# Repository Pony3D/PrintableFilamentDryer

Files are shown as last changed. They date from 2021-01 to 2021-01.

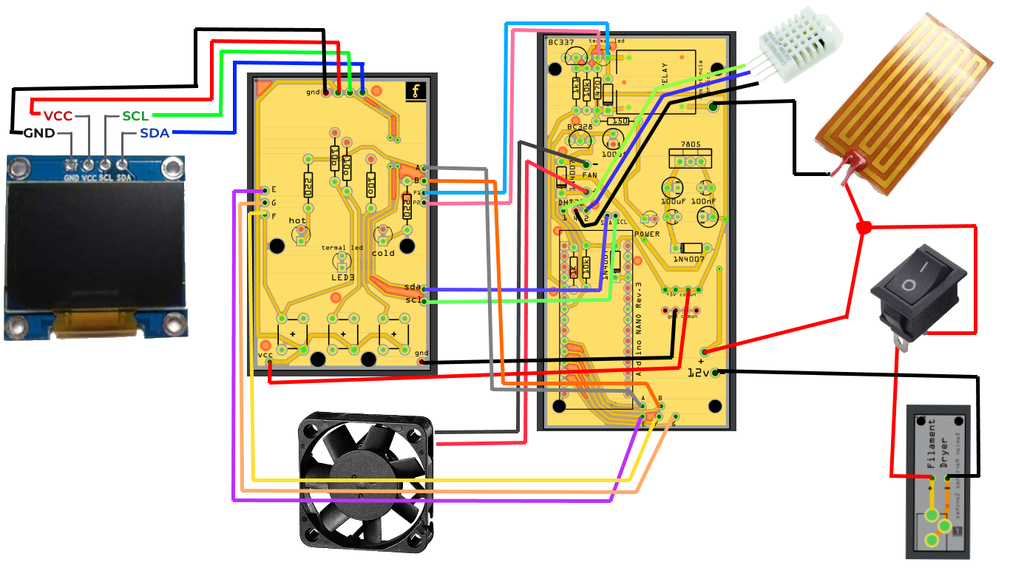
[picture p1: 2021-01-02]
diagrama.png

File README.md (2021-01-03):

# Secador de Filamento Electronico.

Version imprimible de un secador de filamento para impresora 3D.
Modelo optimizado para imprimir en impresora tamaño standar con cama de 220x220, como Ender3.
Es necesario Arduino NANO y conocimientos basicos de electronica.

¿Como funciona?

El secador consta de varias partes que se unen entre si mediante tornillos, ademas de una parte electronica programada en Arduino.
Es recomendable utilizar cables de 1 a 1.3mm maximo de diametro. La electronica es muy simple y cada cable o componente esta marcado con letras y posiciones.

Si se mantiene pulsado el boton +, o el boton -, durante un segundo, se entra en el menu de temperatura, donde se puede configurar la temperatura maxima a alcanzar.
Pulsando repetidas veces sobre + o -, selecionamos la temperatura y pulsando el boton S (Almacenar o Stored), se graba la temperatura de control en la memoria, para el proximo arranque.
El elemento calefactable y el ventilador se encienden si la humedad no esta por debajo del 12%, en el momento que se excede la temperatura maxima grabada en la memoria el elemento calefactable se apaga, no el ventilador.
En el momento que se alcanza un valor de humedad del 12% o inferior, el ventilador y el elemento calefactable se detienen y se muestra, en pantalla, el mensaje de "Secado OK, o DRY OK", y el filamento esta listo para imprimir.
La potencia del elemento calefactable es baja, entorno 14W, por lo que el tiempo de secado del filamento puede ser entorno las 4 horas.
Es recomendable tapar los agujeros exteriores con silicona caliente de los tornillos para mantener la temperatura y humedad correcta del interior.

Componentes necesarios:
- Adaptador de corriente 220v/12v (1.5 a 3A max). https://es.aliexpress.com/item/32859196804.html
- Elemento calefactable de polyamida (12v 14W). https://es.aliexpress.com/item/4000603792416.html
- Interruptor. https://es.aliexpress.com/item/32627544552.html
- Rodamientos de bolas MR106ZZ (6x10x3). https://es.aliexpress.com/item/4000013719586.html
- Ventilador silencioso 40x40x10 12v: https://www.amazon.es/gp/product/B01HTFG9RG/ref=ppx_yo_dt_b_asin_title_o06_s00?ie=UTF8&psc=1
- 0.96" I2C OLED 2 colores. https://es.aliexpress.com/item/1005001392369794.html
- DHT22 (No utilizar DHT11). https://es.aliexpress.com/item/32716996619.html
- Arduino NANO. https://es.aliexpress.com/item/32788387125.html
- Leds de colores: https://es.aliexpress.com/item/32240262628.html
- Conector DC005: https://es.aliexpress.com/item/4000034340966.html
- Rele 5vdc Arduino (sin PCB): https://es.aliexpress.com/item/33032279721.html
- Pulsadores largos: https://es.aliexpress.com/item/32857436208.html

Componentes electronicos PCB 3:
- Power led: 1 Lila o Verde, color a elegir.
- Resistencia: 1K (x2)
- Resistencia: 10K (x2)
- Resistencia: 470 Ohms (x1)
- Resistencia: 150 Ohms (x1)
- Diodo: 14N007 (x3)
- Transistor: BC337 (x1)
- Transistor: BC328 (x1)
- Mosfet: 7805 (x1)
- Condensador ceramico: 100nf (x2)
- Condensador polarizado: 100uf (x2)
- Rele (tipico arduino) 5v 10A.

Componentes electronicos Panel de Control:
- Leds: x1 Rojo, x1 Naranja, x1 Azul.
- Resistencia: 220 Ohms (x2)
- Resistencia: 10 Ohms (x3)
- Pulsadores: (x3)
- Pantalla OLED 0.96": (x1)

LEDS Panel de Control:
- COLD Led: Azul
- HOT Led: Rojo
- LED3 (thermal led): Naranja

Codigo arduino en Español y Ingles, archivos Gerber y Fritzing, diagramas electronicos, componentes necesarios y mas:
https://github.com/Pony3D/PrintableFilamentDryer

¿Donde fabricar las placas PCB?: 
Por ejemplo; https://jlcpcb.com/

ESTE ES UN PROYECTO OPEN SOURCE, POR LO QUE CUALQUIER ELEMENTO ELECTRONICO O DE PROGRAMACION PUEDE SER MODIFICADO Y MEJORADO, EN REALIDAD, ESPERO QUE LO MEJOREIS ;)

NOTA: Las fotografias del modelo expuesta representan un prototipo sobre el que se hicieron las ultimas mejoras, puede ser distinto del modelo final.

///////////////////////////////// ENGLISH TRANSLATION //////////////////////////////////////

# Electronic Filament Dryer.

Printable version of a filament dryer for 3D printer.
Model optimized for printing on a standard size printer with a 220x220 bed, such as Ender3.
Arduino NANO and basic knowledge of electronics are necessary.

How does it work?

The dryer consists of several parts that are joined together by screws, in addition to an electronic part programmed in Arduino.
It is recommended to use cables with a maximum diameter of 1 to 1.3mm. The electronics is very simple and each wire or component is marked with letters and positions.

If you hold down the + button, or the - button, for one second, you enter the temperature menu, where you can set the maximum temperature to be reached.
Pressing repeatedly on + or -, we select the temperature and pressing the S button (Store or Stored), the control temperature is recorded in the memory, for the next start.
The heating element and the fan turn on if the humidity is not below 12%, when the maximum temperature recorded in the memory is exceeded, the heating element turns off, not the fan.
As soon as a humidity value of 12% or less is reached, the fan and the heating element stop and the message "Drying OK, or DRY OK" is displayed on the screen, and the filament is ready to print. .
The power of the heating element is low, around 14W, so the drying time of the filament can be around 4 hours.
It is recommended to cover the outer holes with hot silicone of the screws to maintain the correct temperature and humidity inside.

Required components:
- 220v / 12v power adapter (1.5 to 3A max). https://es.aliexpress.com/item/32859196804.html
- Polyamide heating element (12v 14W). https://es.aliexpress.com/item/4000603792416.html
- Switch. https://es.aliexpress.com/item/32627544552.html
- MR106ZZ ball bearings (6x10x3). https://es.aliexpress.com/item/4000013719586.html
- Silent fan 40x40x10 12v: https://www.amazon.es/gp/product/B01HTFG9RG/ref=ppx_yo_dt_b_asin_title_o06_s00?ie=UTF8&psc=1
- 0.96 "I2C OLED 2 colors. Https://es.aliexpress.com/item/1005001392369794.html
- DHT22 (Do not use DHT11). https://es.aliexpress.com/item/32716996619.html
- Arduino NANO. https://es.aliexpress.com/item/32788387125.html
- Color LEDs: https://es.aliexpress.com/item/32240262628.html
- DC005 connector: https://es.aliexpress.com/item/4000034340966.html
- 5vdc Arduino relay (without PCB): https://es.aliexpress.com/item/33032279721.html
- Long pushbuttons: https://es.aliexpress.com/item/32857436208.html

Electronic components PCB 3:
- Power led: 1 Purple or Green, color to choose.
- Resistance: 1K (x2)
- Resistance: 10K (x2)
- Resistance: 470 Ohms (x1)
- Resistance: 150 Ohms (x1)
- Diode: 14N007 (x3)
- Transistor: BC337 (x1)
- Transistor: BC328 (x1)
- Mosfet: 7805 (x1)
- Ceramic capacitor: 100nf (x2)
- Polarized capacitor: 100uf (x2)
- Relay (typical arduino) 5v 10A.

Electronic components Control Panel:
- Leds: x1 Red, x1 Orange, x1 Blue.
- Resistance: 220 Ohms (x2)
- Resistance: 10 Ohms (x3)
- Buttons: (x3)
- 0.96 "OLED screen: (x1)

LEDS Control Panel:
- COLD Led: Blue
- HOT Led: Red
- LED3 (thermal led): Orange

Arduino code in Spanish and English, Gerber and Fritzing files, electronic diagrams, necessary components and more:
https://github.com/Pony3D/PrintableFilamentDryer

Where to make PCB boards ?:
For example; https://jlcpcb.com/

THIS IS AN OPEN SOURCE PROJECT, SO ANY ELECTRONIC OR PROGRAMMING ELEMENTS CAN BE MODIFIED AND IMPROVED, IN REALITY, I HOPE YOU WILL IMPROVE IT;)

NOTE: The photographs of the exposed model represent a prototype on which the last improvements were made, it may be different from the final model.

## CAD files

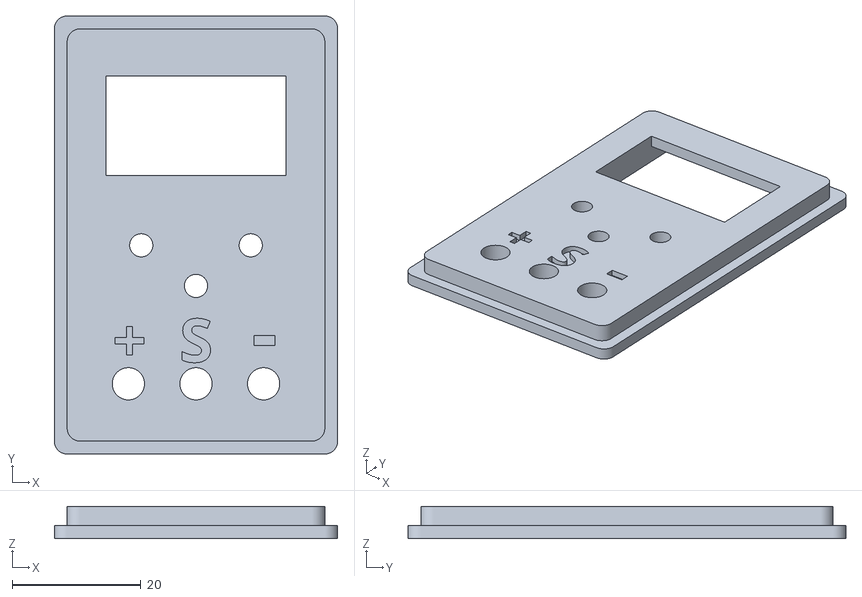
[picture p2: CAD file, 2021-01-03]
Secador Final files/Panel_control_v2.stl
44.0 x 68.0 x 5.00

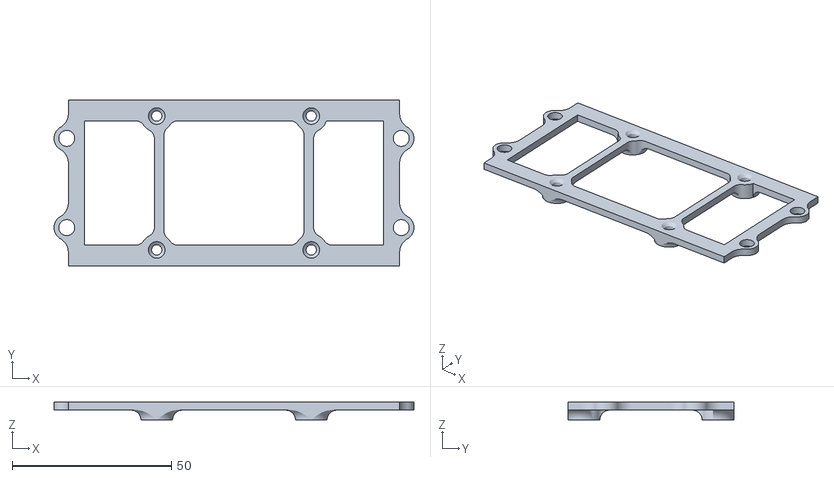
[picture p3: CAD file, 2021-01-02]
Secador Final files/Calefactor - Part 2.stl
113.0 x 52.0 x 5.50

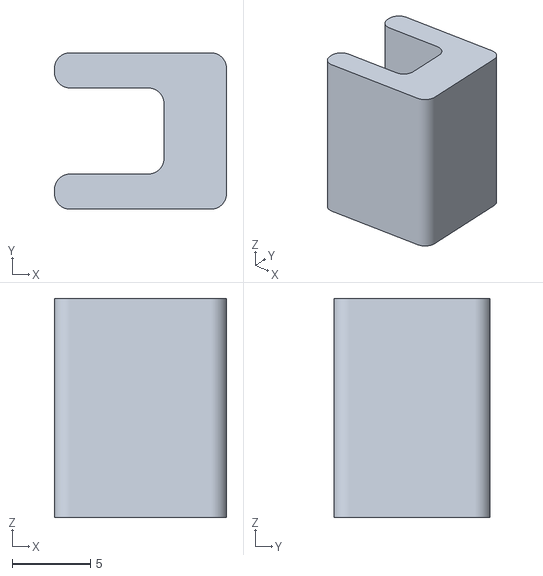
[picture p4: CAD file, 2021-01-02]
Secador Final files/Calefactor - Grapa.stl
11.0 x 10.0 x 14.0

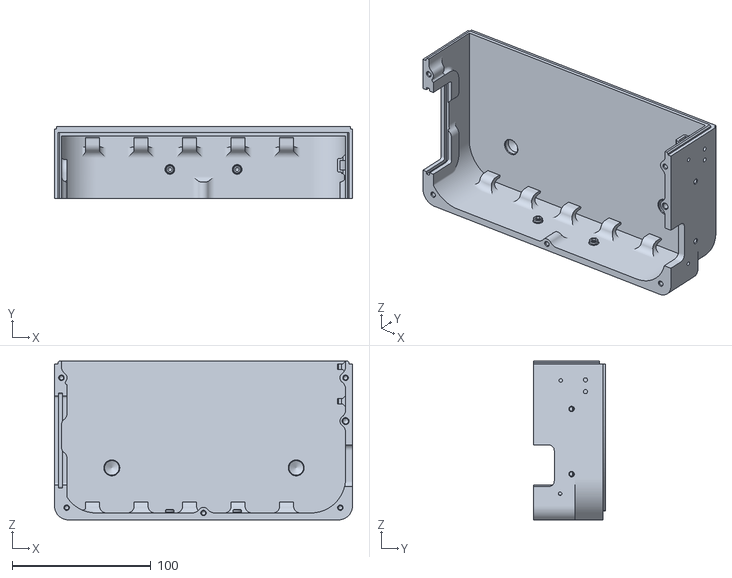
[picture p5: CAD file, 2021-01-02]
Secador Final files/Secador_inferior_IZQ.stl
215.0 x 52.0 x 114.5

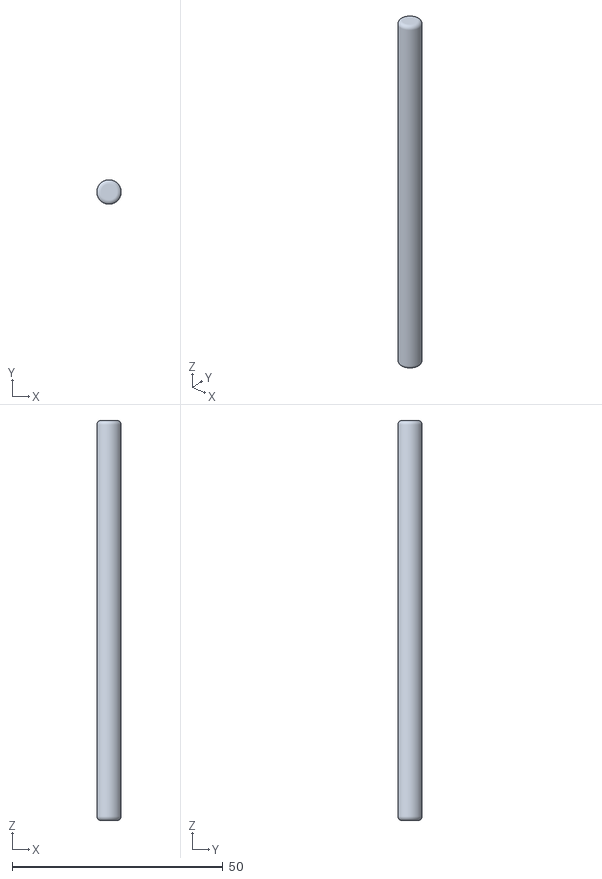
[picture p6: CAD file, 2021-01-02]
Secador Final files/Soporte_rollo_filamento.stl
5.80 x 5.80 x 95.0

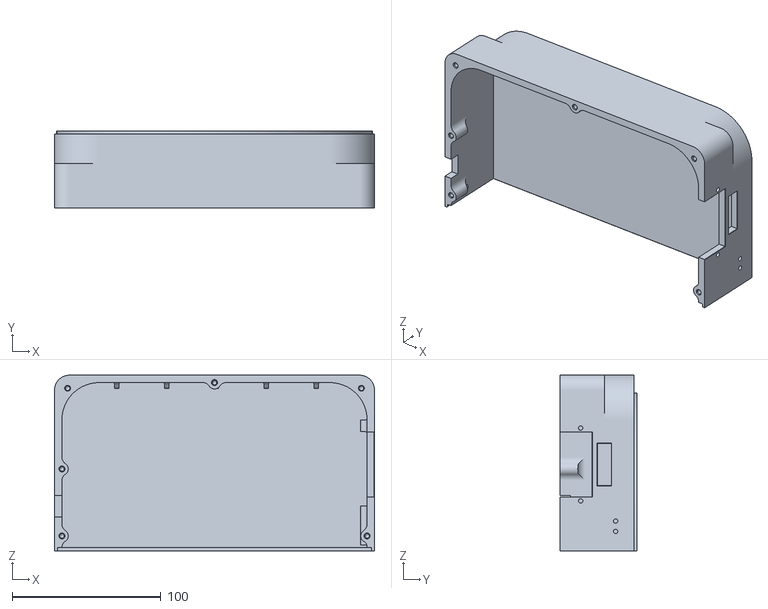
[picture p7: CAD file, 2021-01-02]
Secador Final files/Secador_tapa_IZQ.stl
215.0 x 52.0 x 118.0

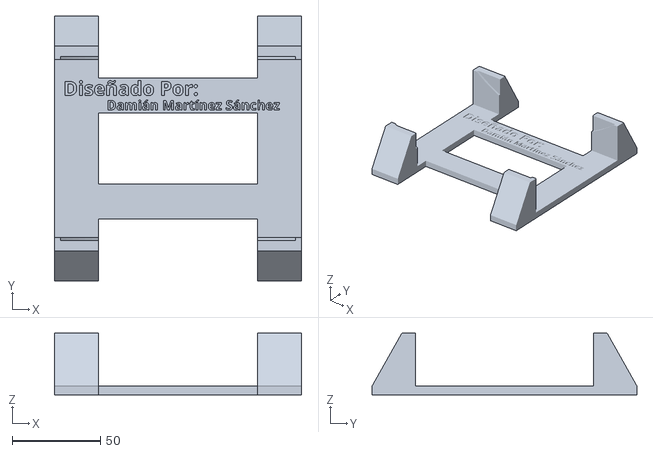
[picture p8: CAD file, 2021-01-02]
Secador Final files/Patas.stl
140.0 x 150.0 x 35.0

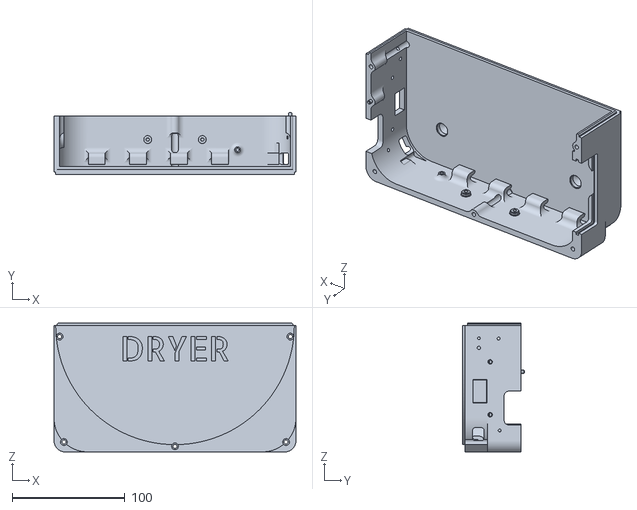
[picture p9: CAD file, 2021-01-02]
Secador Final files/Secador_inferior_DRCHA.stl
215.0 x 55.0 x 114.5

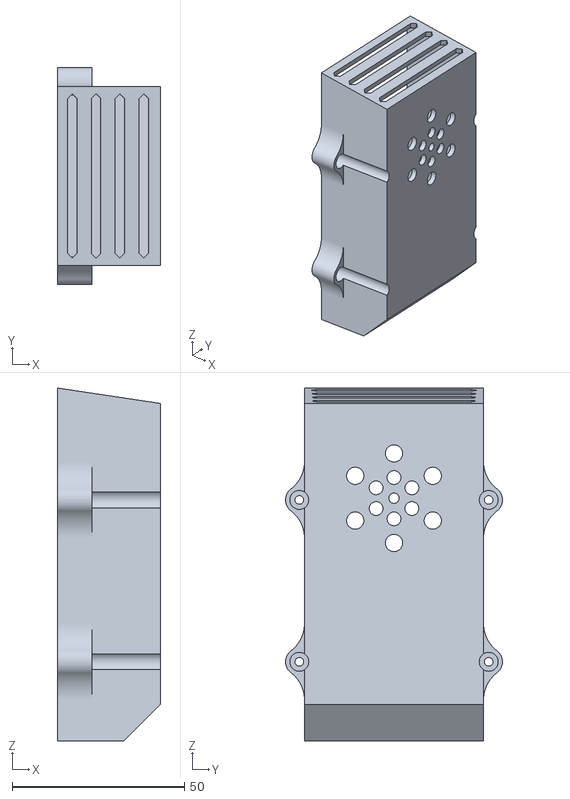
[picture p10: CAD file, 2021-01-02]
Secador Final files/tapa_circuito.stl
30.0 x 63.0 x 102.5

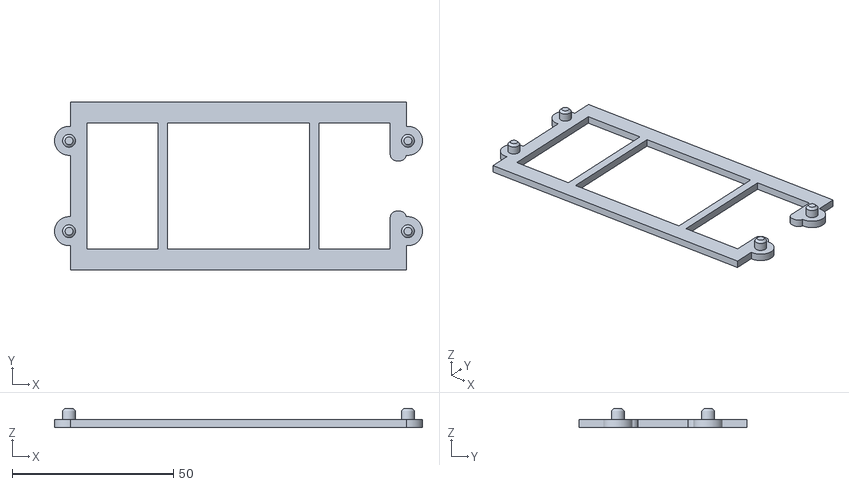
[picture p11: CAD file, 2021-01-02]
Secador Final files/Calefactor - Part 1.stl
114.0 x 52.0 x 6.00

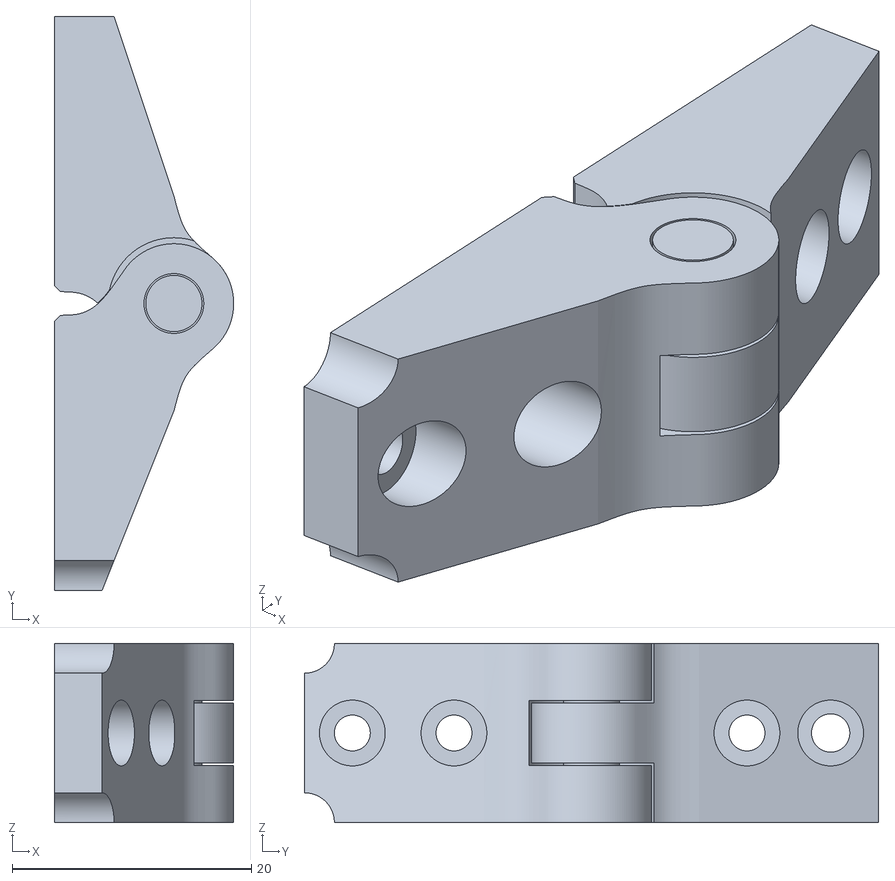
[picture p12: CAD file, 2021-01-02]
Secador Final files/Visagras.stl
15.0 x 48.0 x 15.0

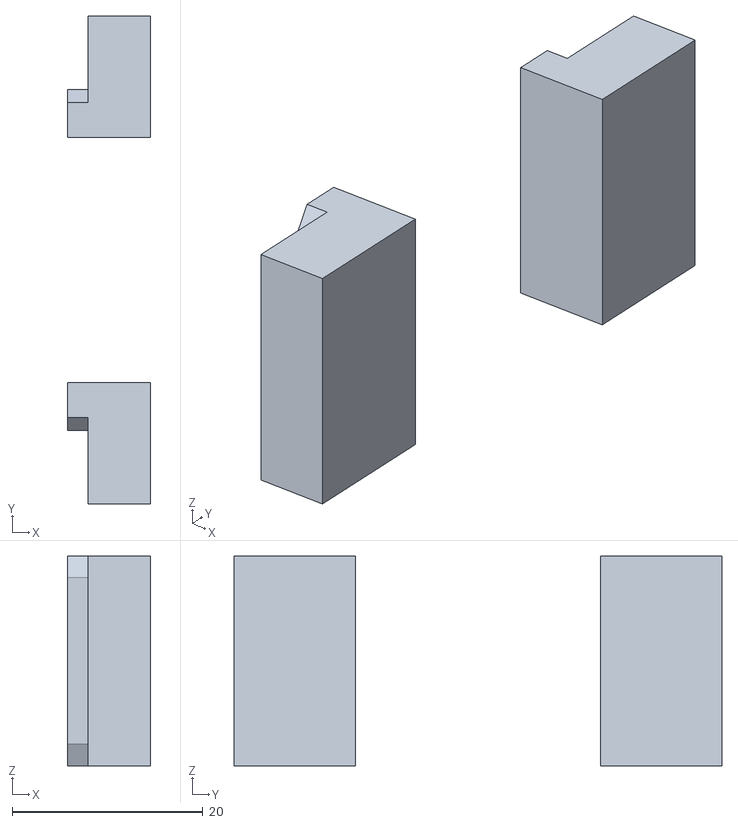
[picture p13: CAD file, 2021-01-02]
Secador Final files/FAN_inside_supports_optional.stl
8.75 x 51.2 x 22.0

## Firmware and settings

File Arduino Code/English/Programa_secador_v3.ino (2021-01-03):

/*###################################################################################################################################
 *  Programa realizado por Damian Martinez Sanchez para el secador de filamento imprimible.
 *  Modificar variables de <CONFIGURACION MANUAL> en funcion del sistema de PCB y sensores utilizados para el secador.
 *  Diseñado para Arduino NANO v.3
 ###################################################################################################################################*/
 
#include <EEPROM.h>
#include <SPI.h>
#include <Wire.h>
#include <DHT.h>
#include <Adafruit_GFX.h>
#include <Adafruit_SSD1306.h>
Adafruit_SSD1306 display(128, 64, &Wire, -1); // Parametros pantalla Oled

const unsigned char bmp1 [] PROGMEM = {
  0x00, 0x00, 0x07, 0xe0, 0x07, 0xe0, 0x01, 0x80, 0x01, 0x80, 0x30, 0x0c, 0x30, 0x0c, 0x3d, 0xbc, 
  0x3d, 0xbc, 0x30, 0x0c, 0x31, 0x8c, 0x01, 0x80, 0x07, 0xe0, 0x07, 0xe0, 0x00, 0x00, 0x00, 0x00
};

const unsigned char bmp2 [] PROGMEM = {
  0x00, 0x00, 0x08, 0x10, 0x18, 0x18, 0x38, 0x1c, 0x7c, 0x3e, 0x0c, 0x30, 0x00, 0x00, 0x01, 0x80, 
  0x01, 0x80, 0x00, 0x00, 0x0c, 0x30, 0x7c, 0x3e, 0x38, 0x1c, 0x18, 0x18, 0x08, 0x10, 0x00, 0x00
};


const int DHTPIN = 4; //Sensor de Lecturas DHT
const int relay = 2; // Rele de la Resistencia termica de 12v
const int fan = 5; // Ventilador PCB 2
const int coldled = 8; //Led Frio - B
const int warmled = 7; //Led Caliente - A
const int store = 11; //Boton Almacenar - G
const int Bmenos = 10; //Boton menos - F
const int Bmas = 9; //Boton mas - E



//########################################################################################
//################################ <CONFIGURACION MANUAL> ################################
//########################################################################################

 
#define DHTTYPE DHT22 // Definir tipo de sensor DHT11 o DHT22
int AONOFF = 1; // 1 = Ventilador encendido 100% // 0 = Ventilador encendido al 50%
int Tmax = 55; // Temperatura maxima (excederse en la temperatura maxima podria dañar componentes expuestos al calor directo).
int Tmin = 23; // Temperatura minima (no menos a la temperatura ambiente).


/////////////////////////////// <FIN CONFIGURACION MANUAL> ///////////////////////////////

 
DHT dht(DHTPIN, DHTTYPE);
float TMP = dht.readTemperature();
float HUM = dht.readHumidity();
int Hcontrol = 12; // Humedad de secado por defecto (El filamento debe estar entre un 10 y 13% de humedad)
float T = 2.55;  // Multiplicador velocidad del ventilador de 12v.
int pulso;
int ultimo_pulso;
int Tcontrol = EEPROM.read(3);
int Tbucle = 0; // Control de bucle principal
int letargo = 0; // Control de bucle secundario

void setup() {

  Serial.begin(9600);
  dht.begin();
  pinMode(fan, OUTPUT);
  pinMode(relay, OUTPUT);
  pinMode(coldled, OUTPUT);
  pinMode(warmled, OUTPUT);
  pinMode(DHTPIN, INPUT);
  pinMode(store, INPUT);
  pinMode(Bmenos, INPUT);
  pinMode(Bmas, INPUT);
  
// Iniciar Oled, si falla, mostrar error. Repetir bucle. Led alarma 2 destellos por segundo.
    if (!display.begin(SSD1306_SWITCHCAPVCC, 0x3C)) {
    Serial.println("Display not found.");
    for(;;);
 }
  display.clearDisplay();
  display.setTextSize(1);
  display.setTextColor(SSD1306_WHITE);
  display.setCursor(0, 16);
  display.println("Loading EEPROM...");
  display.display();
  delay(500);

// Comprobar si esta grabado el control de arranque (posicion 0 de la memoria), si no, grabar variables en memoria.

  if (EEPROM.read(0) != 1) { // Control de arranque para grabar por primera y unica vez las variables cuando se instale el programa
      EEPROM.write(0, 0); 
      EEPROM.put(1, AONOFF);
      EEPROM.put(3, 30);
  }
  display.setTextSize(1);
  display.setTextColor(SSD1306_WHITE);
  display.setCursor(0, 25);
  display.println("Reading DHT...");
  display.display();  
  delay(500);

// Comprobar lecturas del DHT. Si falla mostrar error, repetir bucle. Led alarma 1 destello por segundo.  
 
  if (isnan(dht.readTemperature()) || isnan(dht.readHumidity())) {
  display.setTextSize(1);
  display.setTextColor(SSD1306_WHITE);
  display.setCursor(0, 35);
  display.println("Error Reading DHT.");
  display.display(); 
   for(;;); // Si falla la lectura detiene el programa
  } else {
  display.setTextSize(1);
  display.setTextColor(SSD1306_WHITE);
  display.setCursor(0, 35);
  display.println("DHT OK.");
  display.display();  
  delay(1000);
  }
}

void loop() {
  
  display.clearDisplay();

//###########################################################################
//################ INICIAR DE LECTURAS ###############################
//###########################################################################


    TMP = dht.readTemperature();
    HUM = dht.readHumidity();
    
//////////////////// FIN CONTADOR DE LECTURAS /////////////////////


//##########################################################################################
//############## INICIANDO PANTALLA PRINCIPAL OLED 128x64 2 zonas Bicolor ##################
//##########################################################################################
  if (HUM >= Hcontrol) {
   displaymenu();
   secando1();
  }
  else {
   displaymenu();
   secado();
  }
  
///////////////////////////// FIN Parte.1 PANTALLA PRINCIPAL /////////////////////////////

//########################################################################################## 
//######################### INICIANDO CONTROL DE SECADO #########################
//##########################################################################################

 if (HUM >= Hcontrol) { 
  digitalWrite(coldled, HIGH);
    if (AONOFF == 1) { // Determina la velocidad del ventilador, al 100% o al 50%, dependiendo del voltaje aplicado al BC337.
     digitalWrite(fan, HIGH);
  } else {
     digitalWrite(fan, LOW);
}
 }
 else if (HUM <= Hcontrol) {
  digitalWrite(coldled, LOW);
  digitalWrite(warmled, HIGH);
  digitalWrite(relay, LOW);
 }

 
  if (TMP >= Tmax) {
    digitalWrite(relay, LOW);
     } else {
     digitalWrite(relay, HIGH);
 }
 
 // Serial.println(HUM);
 // Serial.println(EEPROM.read(1));
 
///////////////////////////// FIN CONTROL AUTOMATICO DE SECADO /////////////////////////////////

//#######################################################################################
//######################### CONTROL DE ENTRADA DE MENUS #################################
//#######################################################################################

if (digitalRead(Bmas) == 1) { Tbucle = 1; }
if (digitalRead(Bmenos) == 1) { Tbucle = 1; }
if (digitalRead(store) == 1) { Tbucle = 3; } 
   
///////////////////// SUBIR TEMPERATURA ////////////////////////////

if (Tbucle == 1) { // Bucle mantener control de menus de temperatura en pantalla
  while (Tbucle == 1) {
  display.clearDisplay();
  
if (digitalRead(Bmas) == 1) { 
  while (digitalRead(Bmas) == 1) { letargo = 2; }
   while (letargo == 2) { // Bucle mantener menu subir temperatura
     
  if (digitalRead(Bmas) == 1) {
    while(digitalRead(Bmas) == 1){
  display.clearDisplay();
  display.fillTriangle(30, 18, 10, 58, 50, 58, SSD1306_WHITE);
  displaytemp();
  display.display();
      }
      if (Tcontrol < Tmax) {
           ++Tcontrol;
        }
   }
  else if (digitalRead(Bmas) == 0) {
  display.clearDisplay();
  display.drawTriangle(30, 18, 10, 58, 50, 58, SSD1306_WHITE);
  displaytemp();
  display.display(); 
   }
   if (digitalRead(Bmenos) == 1) { letargo = 1; } // Si se activa, salir del bucle subir y saltar al bucle bajar
   if (digitalRead(store) == 1) {
    grabardatos();
    letargo = 0;
    Tbucle = 0;
    }
  } // Fin bucle mantener menu subir temperatura 
}

///////////////////// BAJAR TEMPERATURA ////////////////////////////
    
if (digitalRead(Bmenos) == 1) {
  while (digitalRead(Bmenos) == 1) { letargo = 1; }
  while (letargo == 1) {
      
  if (digitalRead(Bmenos) == 1) {
    while(digitalRead(Bmenos) == 1){
  display.clearDisplay();
  display.fillTriangle(10, 18, 50, 18, 30, 58, SSD1306_WHITE);
  displaytemp();
  display.display();
      }
       if (Tcontrol > Tmin) {
            --Tcontrol;
        }  
   }
  else if (digitalRead(Bmenos) == 0) {
  display.clearDisplay();
  display.drawTriangle(10, 18, 50, 18, 30, 58, SSD1306_WHITE);
  displaytemp();
  display.display(); 
   }
   if (digitalRead(Bmas) == 1) { letargo = 2; }
   if (digitalRead(store) == 1) {
    grabardatos();
    letargo = 0;
    Tbucle = 0;
    }
  }
 }
}
}

///////////////////// FIN MENU CONTROL TEMPERATURA ////////////////////////////

////////////////////////// MENU CONFIGURACION VENTILADOR //////////////////////////////

if (Tbucle == 3) {
  while (digitalRead(store) == 1) {} 
  while (Tbucle == 3) { // Bucle mantener menu FAN en pantalla
      display.clearDisplay();
         menufan();
         display.display();
  if (digitalRead(Bmas) == 1) {
    while (digitalRead(Bmas) == 1) {} // Retorno del boton
           if (AONOFF < 1) {
            ++AONOFF;     
        }
        else { --AONOFF; }
       Serial.println(AONOFF);
  }

if (digitalRead(store) == 1) {
  while(digitalRead(store) == 1) {} // Retorno del boton
    display.setTextSize(1);
    display.setTextColor(SSD1306_WHITE);
    display.setCursor(5,50);
    display.println("Writing EEPROM...");
    display.display();
    EEPROM.update(1, AONOFF);
    delay(2000);
    display.clearDisplay();
      Tbucle = 0;
   }
  }
 }

////////////////////////////// FIN MENU VENTILADOR //////////////////////////////////

  if (HUM >= Hcontrol) {
   displaymenu();
   secando2();
  }
  else {
   displaymenu();
   secado();
  }

 display.clearDisplay();
 
} // FIN DEL PROGRAMA

void grabardatos() {
  while (digitalRead(store) == 1) {}
    display.clearDisplay();
    display.setTextSize(2);
    display.setTextColor(SSD1306_WHITE);
    display.setCursor(0,0);
    display.println("EEPROM.");
    display.setTextSize(2);
    display.setTextColor(SSD1306_WHITE);
    display.setCursor(0, 20);
    display.print("Stored ");
    display.print("Temp. ");
    display.print(Tcontrol);
    display.cp437(true);
    display.write(167);
    display.display();
   EEPROM.update(3, Tcontrol);
  delay(2000);
  display.clearDisplay();
 }

void displaytemp() {
  display.setTextSize(2);
  display.setTextColor(SSD1306_WHITE);
  display.setCursor(0,0);
  display.println("Menu Temp.");
  display.setTextSize(3);
  display.setTextColor(SSD1306_WHITE);
  display.setCursor(70, 30);
  display.println(Tcontrol);
}

void displaymenu() {
  display.clearDisplay();
  display.drawRect(0, 16, 128, 48, SSD1306_WHITE);
  display.drawLine(0, 39, 128, 39, SSD1306_WHITE);
  display.setTextSize(2);
  display.setTextColor(SSD1306_WHITE);
  display.setCursor(5,20);
  display.print("Temp ");
  display.print(TMP);
//  display.cp437(true);
//  display.write(167);
  display.setCursor(5,43);
  display.print("Humi ");
  display.print(HUM);
 // display.cp437(true);
 // display.write(37);
}


void secando1() {
  display.setTextColor(SSD1306_WHITE);
  display.setCursor(0,0);
  display.print("Drying");
  display.drawBitmap(112, 0, bmp1, 16, 16, SSD1306_WHITE);
  display.display();
  delay(250);
}

void secando2() {
  display.setTextColor(SSD1306_WHITE);
  display.setCursor(0,0);
  display.print("Drying");
  display.drawBitmap(112, 0, bmp2, 16, 16, SSD1306_WHITE);
  display.display();
  delay(250);
}

void secado() {
  display.setTextColor(SSD1306_WHITE);
  display.setCursor(0,0);
  display.print("DRY OK.");
  display.display();
  delay(10);
}

void menufan() {
    display.setTextSize(2);
    display.setTextColor(SSD1306_WHITE);
    display.setCursor(0,0);
    display.println("FAN Menu");
    display.setTextSize(2);
    display.setTextColor(SSD1306_WHITE);
    display.setCursor(0,25);
    display.print("Speed ");
    if (AONOFF == 1) {
    display.print("50");
    display.cp437(true);
    display.write(37);
    }
    else {
    display.print("100");
    display.cp437(true);
    display.write(37);
      }
}

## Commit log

2021-01-02 PCB's Gerber Files
    Ficheros Gerber para imprimir las placas PCB.
2021-01-02 Fritzing PCB's Projects
    [PCB_3.0.fzz, conector_12v.fzz, panel_control.fzz]
2021-01-02 Printable Filament Dryer STL's files.
    [Calefactor - Grapa.stl, Calefactor - Part 1.stl, Calefactor - Part 2.stl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]
2021-01-02 Gerber files for PCB production.
2021-01-02 Fritzing PCB's
    [PCB_3.0.fzz, conector_12v.fzz, panel_control.fzz]
2021-01-02 Wiring Conection Diagram
2021-01-03 Arduino source codes EN/SP
2021-01-03 PCB Updated, pcb 3.0 is obsolete, use 3.1.
2021-01-03 Board update. Use PCB 3.1
    [PCB_3.1.fzz]
2021-01-03 Last Update Arduino Code EN/ES
